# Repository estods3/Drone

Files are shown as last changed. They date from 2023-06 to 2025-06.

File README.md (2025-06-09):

# Quadcopter with ROS/Wifi Flight Controller
This project is for a quadcopter using a WiFi controlled flight controller that you can control from your phone. The flight controller also interfaces with Robotic Operating System (ROS) to support live debugging and data logging with open-sourced industry tools.

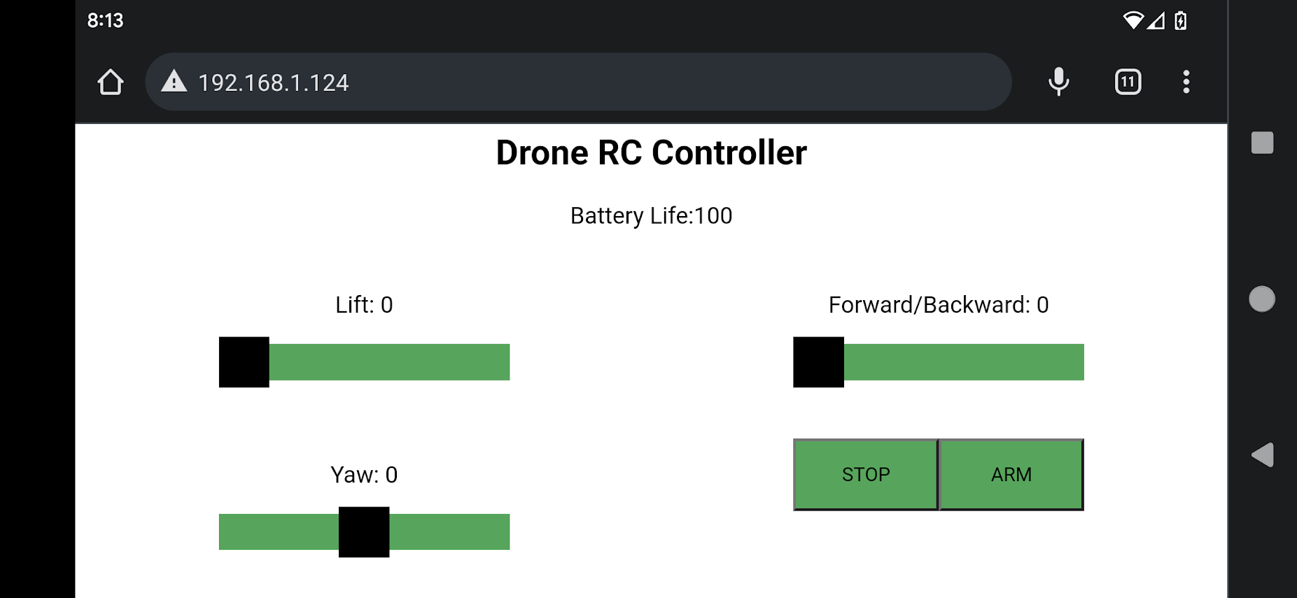
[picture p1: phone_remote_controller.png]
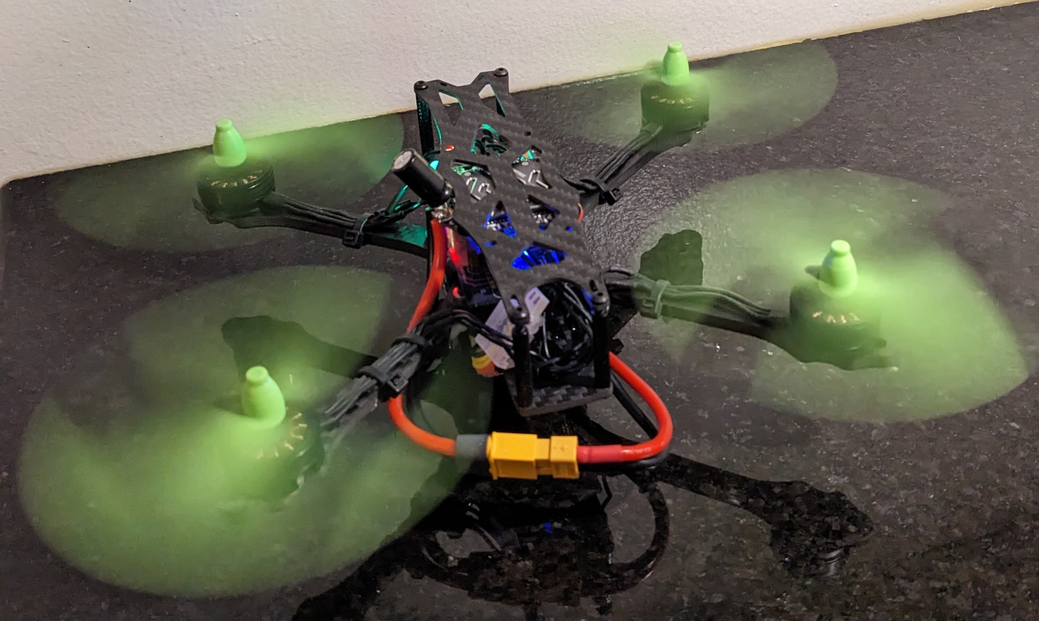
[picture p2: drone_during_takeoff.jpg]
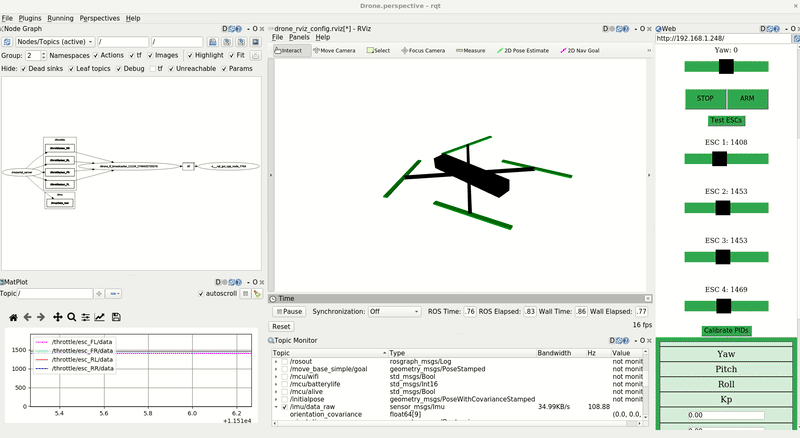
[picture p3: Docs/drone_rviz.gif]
&nbsp;&nbsp;&nbsp;&nbsp;&nbsp;&nbsp;

&nbsp;&nbsp;&nbsp;&nbsp;&nbsp;&nbsp;&nbsp;&nbsp;&nbsp;&nbsp;&nbsp;&nbsp;&nbsp;&nbsp;&nbsp;*Control from Phone/Web, Send Commands to Drone, View data live using ROS*

This repo provides the design files for the custom flight controller hardware and software as well as a parts list for building a working quadcopter with the custom flight controller.

## Flight Controller
The flight controller is a single-board design with accelerometers, microcontroller, wifi, battery monitoring, ESC connector, and status LEDs.

| Top | Bottom |
|---|---|
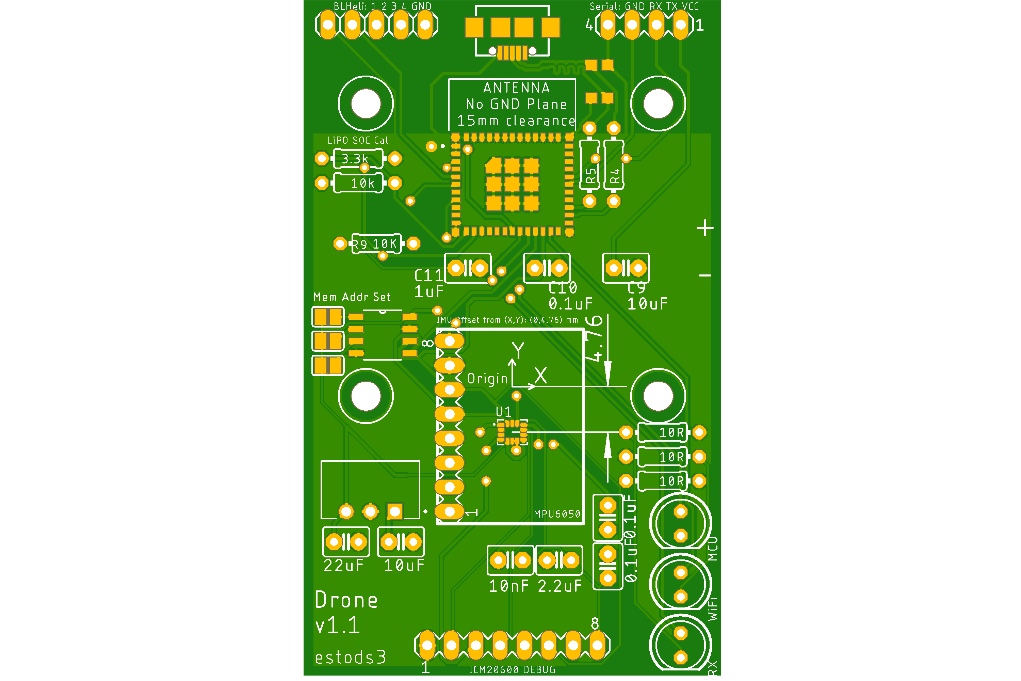
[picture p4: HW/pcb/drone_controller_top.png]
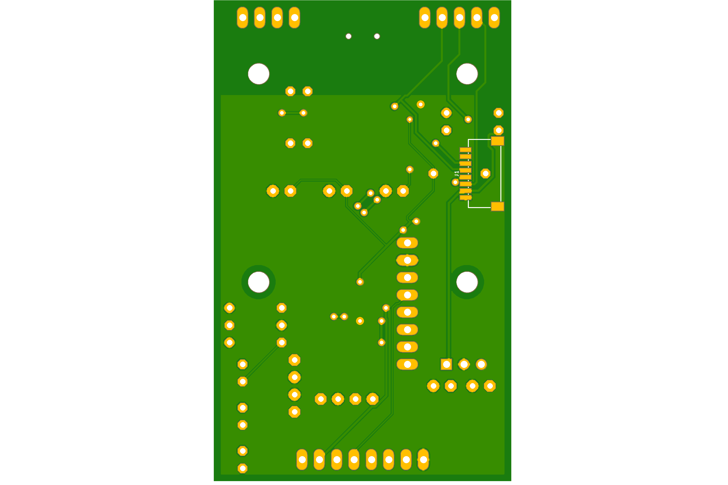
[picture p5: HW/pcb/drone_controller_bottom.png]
|  |  |

Gerber files used to order this PCB are included in the latest release, [here](https://github.com/estods3/Drone/releases/tag/V1.0)

Parts list to assembly final board can be found in the BOM, [here](https://github.com/estods3/Drone/blob/main/HW/BOM.md)

### Hardware Features:
1. 2-Layer design with top and bottom ground plane.
2. Antenna clearance complies with ESP32 specification to help prevent interference to WiFi Signal.
3. IMU orientation aligned with drone frame. Design supports both ISO-20600 and MPU2060 IMU components.

4. Standard 30.5mm by 30.5mm flight controller mounting pattern
5. Eectrical interface using JST-SH 8 Pin connector (compatible with SpeedyBee BL32 50A V3 ESC for stacked ESC/Flight Controller layout).
6. Single Supply (3S LiPo) powering both ESC as well as flight controller (Powered through JST-SH Connector).
7. Status LEDs to quickly see if Wifi is connected, if software is recieving commands from remote controller, etc.
8. Built-in ESC Firmware debug interface with BLHeli Suite (Coming Soon).

### Software Features:
1. Arduino-based C++.
2. Wifi controlled using a phone with browser, provides battery life status as well as controls for Up, Down, Left, Right, etc.
3. Robotic Operating System (ROS) interface provides live feed of IMU data, flight controller status, user commands, and ESC throttle to each motor. (must have variable USE_ROS = True).
4. PID-based flight stability controller (Coming Soon).
5. "Testing Mode" allows user to test throttle of each motor, calibrate PID controller without reflashing flight controller (Coming Soon).

#### IMU Calibration:
Run script to compute IMU calibration:

```
Reading sensors for first time...
Results of measurements a/g:	0.23	0.53	12.09	-0.03	-0.02	0.01

Calculating offsets...
Results of measurements a/g:	-0.00	-0.00	9.81	0.00	0.00	0.00
...

Calibration successful!
Results of measurements a/g:	-0.01	0.00	9.81	0.00	0.00	-0.00

FINISHED!

Sensor readings with offsets:	-0.01	0.00	9.81	0.00	0.00	-0.00
Your offsets:	-0.23	-0.53	-2.29	0.03	0.02	-0.01
```

#### ROS Interface:
Create a ROS interface where you can view and log data from your quadcopter live.

From a PC with ROS installed, run:

```
roscore
```

In another terminal from PC run:

```
roslaunch rosserial_server socket.launch

```

This will create a rosserial server to interface with the nodeMCU controller.

In another terminal launch:
```
rqt
```

to see the following visualization of your drone's data!



#### User Interface/Remote Control
The UI for remote control is deployed over WiFi to a static IP address accessible to a phone logged on to the Flight Controller's hosted WiFi network.



Commands available:

Up, Down, Left, Right, Forward, Backward, Rotate Left, Rotate Right

If not command is given, the drone will hold in place.

## Prototype
This flight controller was tested with a 5 inch FPV Frame, although other frames could be used with tuning of the flight controller.

#### Test Quadcopter Specs:

Physical Size: ~450 grams, 5 inch FPV

Frame: 

Battery Size: 3S Lipo

Motors: brushless DC

ESC: [Speedybee 4-in-1 ESC](https://www.speedybee.com/speedybee-f7-v3-bl32-50a-4-in-1-esc/)

For full BOM, click [here](https://github.com/estods3/Drone/blob/main/HW/BOM.md)

#### ESC Firmware with BLHeli:
Using Arduino Nano as an interface (4wArduino_Nano__16_MULTIv20005.hex) with ESC plugged into pin D4. The opposite corner motors were set to clockwise and counter-clockwise, respectively. NOTE: this can be done in BLHeli software to correct the direction of the motor if the motor was wired incorrectly to the ESC. Brushless DC motors have 3 wires A, B, and C and the order determines the direction.

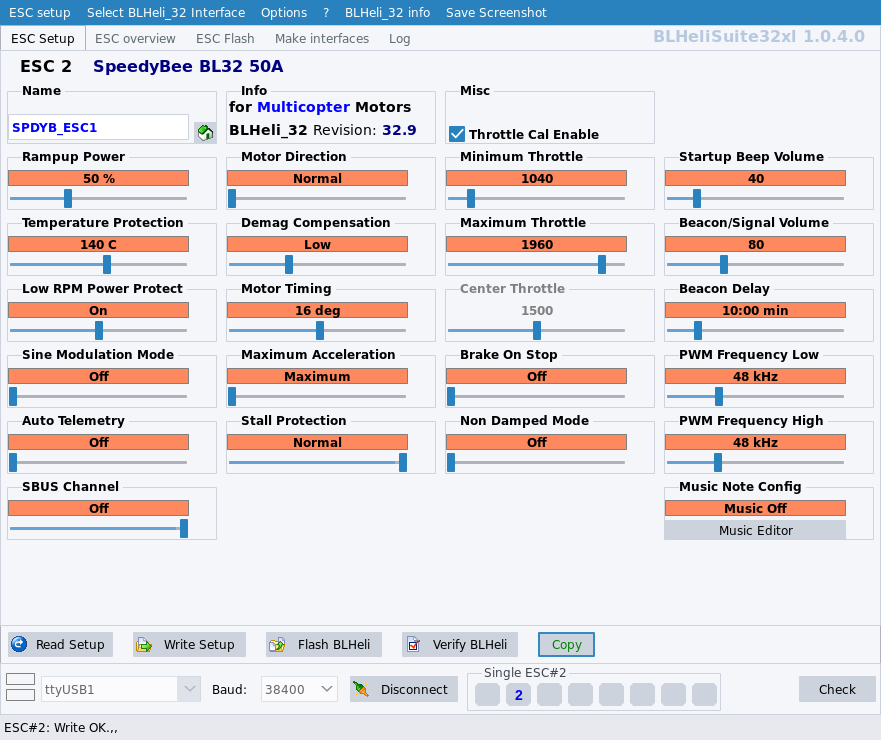
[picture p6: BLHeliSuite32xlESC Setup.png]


## Resources:
PID Controller: 
https://github.com/0xekez/arduino-drone-pid/blob/master/pid_v2_in_arduino/pid_v2_in_arduino.ino
https://www.youtube.com/watch?v=hGcGPUqB67Q
https://www.youtube.com/watch?v=wkfEZmsQqiA
https://github.com/bolandrm/rmb_multicopter

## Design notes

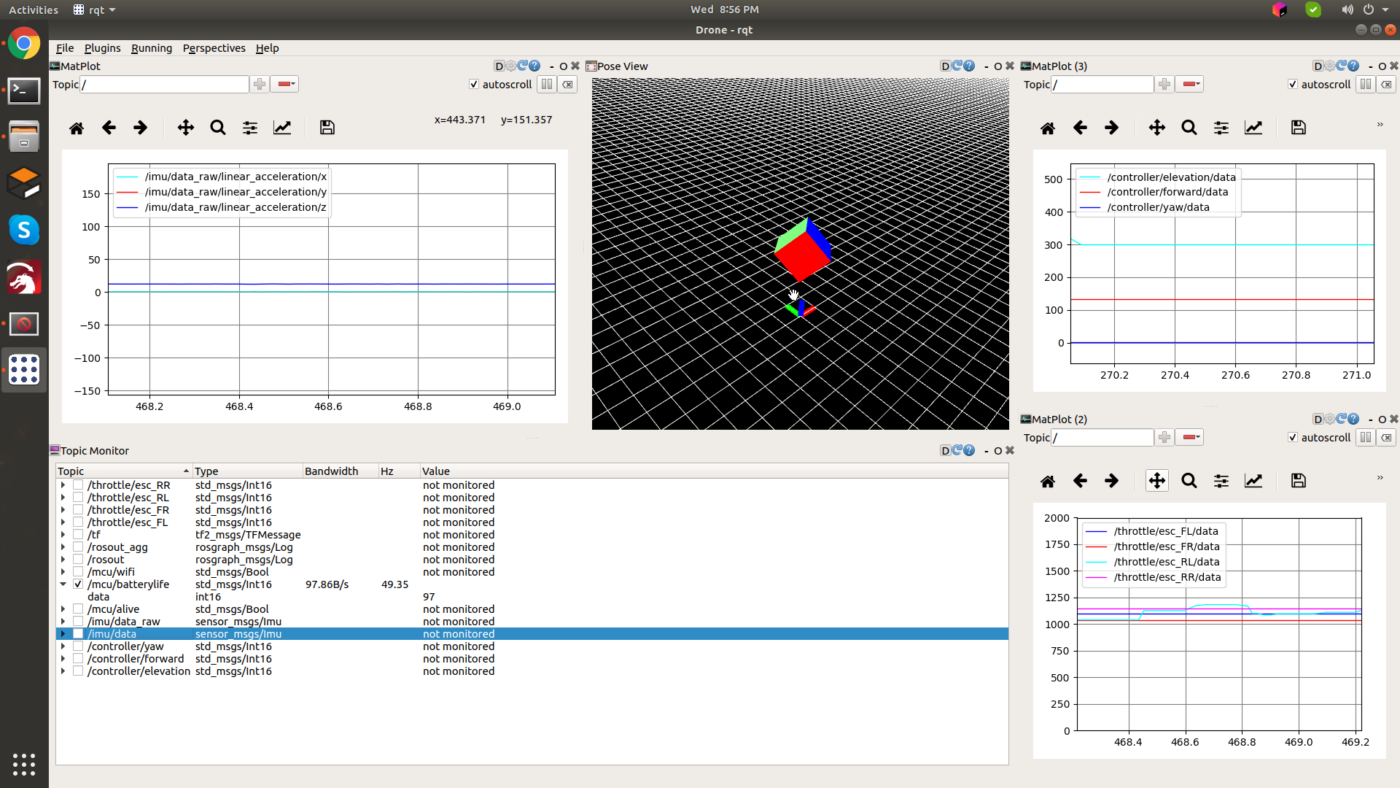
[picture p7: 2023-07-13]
ros_live_visualization.png

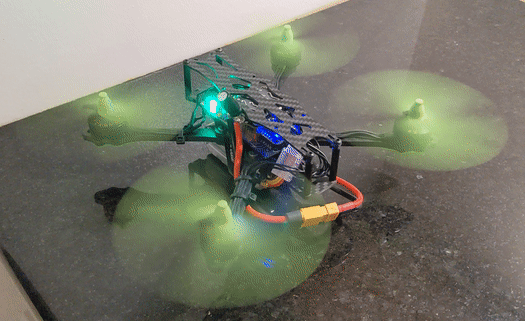
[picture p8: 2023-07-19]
drone.gif

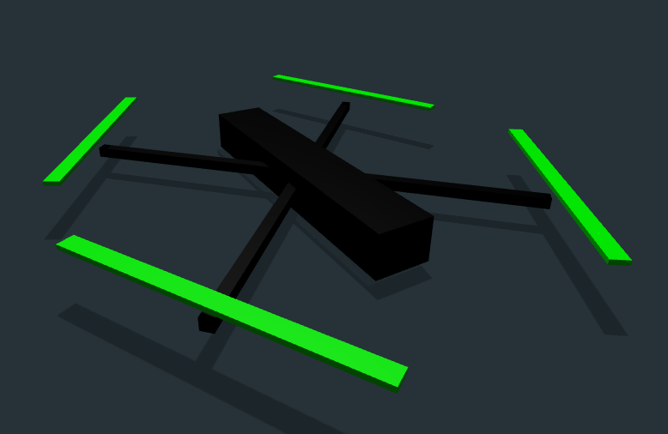
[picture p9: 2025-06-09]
Docs/drone_urdf.png

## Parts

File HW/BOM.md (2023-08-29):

# Bill of Materials

## Powertrain Parts
| Name | Link | Quantity | Part Cost |
| :--- | :--- | :--- | :---- |
| 4-in-1 ESC | [Speedybee](https://www.speedybee.com/speedybee-f7-v3-bl32-50a-4-in-1-esc/) | 1 | $62.99 |
| 3S LiPo Battery | [Amazon - 2 pack](https://www.amazon.com/dp/B07Y67MKQB?psc=1&ref=ppx_yo2ov_dt_b_product_details) | 1 | $30.59 |
| Motors | [Amazon - 4 pack](https://www.amazon.com/dp/B07ZCL45RR?psc=1&ref=ppx_yo2ov_dt_b_product_details) | 4 | $35.99 |
| Propellers | [HobbyKing - 4 pack](https://hobbyking.com/en_us/diatone-5030-plastic-self-tightening-propellers-5-x-3-cw-ccw-green-2-pairs.html) | 4 | $0.67 |
| TOTAL: | | | $130.24 |

## Flight Controller Parts

| Name | Link | Quantity | Part Cost |
| :--- | :--- | :--- | :---- |
| 3.3V Voltage Regulator | [Digikey](https://www.digikey.com/en/products/detail/cui-inc/PXO7803-500-S/16927860) | 1 | $1.41 |
| ESP32 | [Digikey](https://www.digikey.com/en/products/detail/espressif-systems/ESP32-C3-MINI-1-N4/13877574) | 1 | $1.80 |
| IMU1 - ISO20600 | [Digikey](https://www.digikey.com/en/products/detail/tdk-invensense/ICM-20600/8544628) | 1 | $5.67 |
| IMU2 - MPU6050 | [Amazon](https://www.amazon.com/WWZMDiB-Module%EF%BC%883-Axis-Gyroscope-Acceleration%EF%BC%89IIC-Transmission/dp/B0BTKW7K1B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) | 1 | $9.99 |
| JST-SH 8 pin | [HobbyKing - 5 pack](https://hobbyking.com/en_us/jst-sh-8pin-socket-surface-mount-5pcs.html) | 1 | $0.72 |
| micro USB | [Digikey](https://www.digikey.com/en/products/detail/amphenol-cs-fci/10118192-0001LF/2785387) | 1 | $0.40 |
| Memory | [Digikey](https://www.digikey.com/en/products/detail/stmicroelectronics/M24C02-WMN6TP/1663568) | 1 | $0.17 |
| 8-pin header |  | 2 |  |
| 5MM LED |  | 3 |  |
| 10 Ohm Resistor |  | 3 |  |
| 3.3k Ohm Resistor |  | 1 |  |
| 10k Ohm Resistor |  | 1 |  |
| 0.1uF Capacitor |  | 2 |  |
| 10uF Capacitor |  | 1 |  |
| 10nF Capacitor |  | 1 |  |
| 2.2uF Capacitor |  | 1 |  |
| 22uF Capacitor |  | 1 |  |
| TOTAL: |  |  | $20.00 |

NOTE: PCB costs ~$10.00/board to print (Source: Oshpark)

## Frame Parts

| Name | Link | Quantity | Part Cost |
| :--- | :--- | :--- | :---- |
| FPV Racing Drone Frame 5 inch | [Amazon](https://www.amazon.com/gp/product/B071HL5V3H/ref=ppx_yo_dt_b_asin_title_o00_s00?ie=UTF8&psc=1) | 1 | 31.99 |

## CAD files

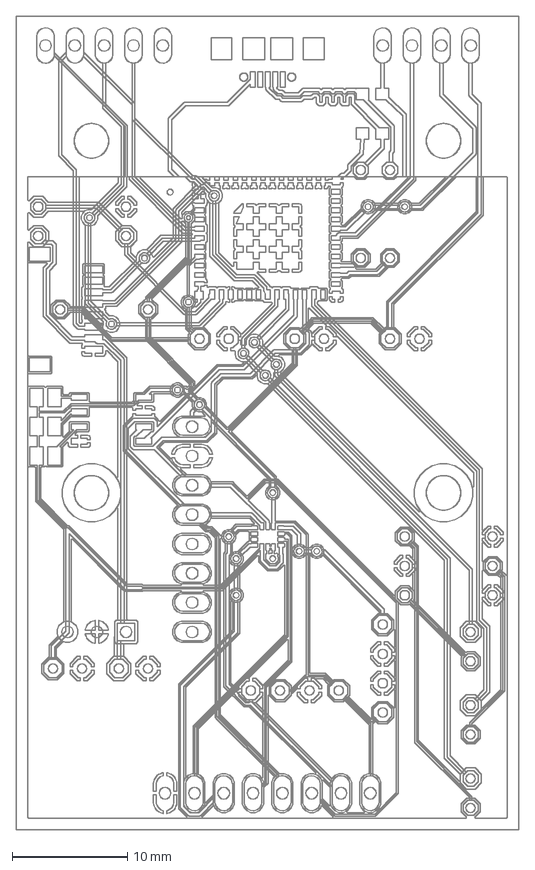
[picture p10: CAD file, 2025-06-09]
HW/pcb/drone_controller_bottom.dxf
43.5 x 70.5 mm

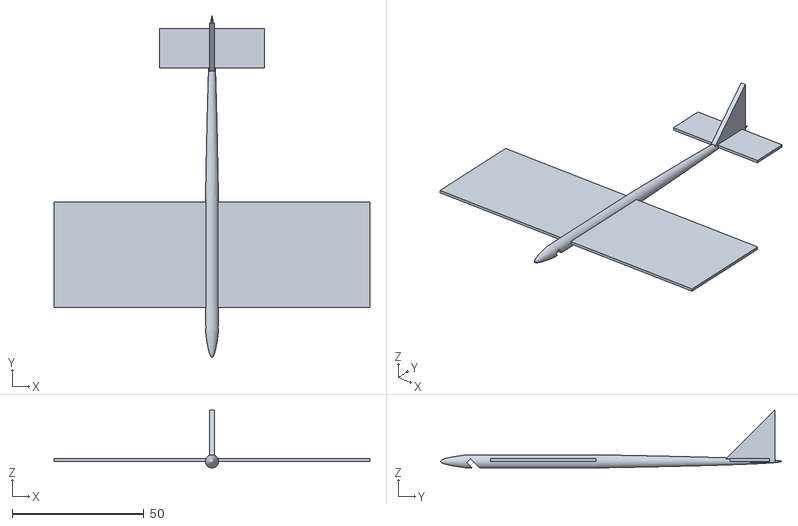
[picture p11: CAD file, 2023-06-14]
SW/orientations_from_IMU_MPU_6050/src/mpu_6050_driver/mesh/FUGMJ38JX8T7E5A.stl
120.0 x 129.5 x 22.0

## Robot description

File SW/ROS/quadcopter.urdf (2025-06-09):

<?xml version="1.0"?>
<robot name="quadcopter_x">

  <!-- Base Link (Main Body) -->
  <link name="base_link">
    <visual>
      <origin xyz="0 0 0" rpy="0 0 0"/>
      <geometry>
        <box size="0.15 0.0254 0.02"/>
      </geometry>
      <material name="body_material">
        <color rgba="0.0 0.0 0.0 1.0"/>
      </material>
    </visual>
    <collision>
      <origin xyz="0 0 0" rpy="0 0 0"/>
      <geometry>
        <box size="0.15 0.0254 0.02"/>
      </geometry>
    </collision>
    <inertial>
      <origin xyz="0 0 0" rpy="0 0 0"/>
      <mass value="0.5"/>
      <inertia ixx="0.001" ixy="0" ixz="0" iyy="0.001" iyz="0" izz="0.001"/>
    </inertial>
  </link>

  <!-- Front Right Arm -->
  <link name="arm_front_right">
    <visual>
      <origin xyz="0.055 0 0" rpy="0 0 0"/>
      <geometry>
        <box size="0.11 0.005 0.005"/>
      </geometry>
      <material name="arm_material">
        <color rgba="0.0 0.0 0.0 1.0"/>
      </material>
    </visual>
    <collision>
      <origin xyz="0.055 0 0" rpy="0 0 0"/>
      <geometry>
        <box size="0.11 0.005 0.005"/>
      </geometry>
    </collision>
    <inertial>
      <origin xyz="0.055 0 0" rpy="0 0 0"/>
      <mass value="0.02"/>
      <inertia ixx="0.0001" ixy="0" ixz="0" iyy="0.0001" iyz="0" izz="0.0001"/>
    </inertial>
  </link>

  <!-- Front Left Arm -->
  <link name="arm_front_left">
    <visual>
      <origin xyz="0.055 0 0" rpy="0 0 0"/>
      <geometry>
        <box size="0.11 0.005 0.005"/>
      </geometry>
      <material name="arm_material">
        <color rgba="0.0 0.0 0.0 1.0"/>
      </material>
    </visual>
    <collision>
      <origin xyz="0.055 0 0" rpy="0 0 0"/>
      <geometry>
        <box size="0.11 0.005 0.005"/>
      </geometry>
    </collision>
    <inertial>
      <origin xyz="0.055 0 0" rpy="0 0 0"/>
      <mass value="0.02"/>
      <inertia ixx="0.0001" ixy="0" ixz="0" iyy="0.0001" iyz="0" izz="0.0001"/>
    </inertial>
  </link>

  <!-- Rear Right Arm -->
  <link name="arm_rear_right">
    <visual>
      <origin xyz="0.055 0 0" rpy="0 0 0"/>
      <geometry>
        <box size="0.11 0.005 0.005"/>
      </geometry>
      <material name="arm_material">
        <color rgba="0.0 0.0 0.0 1.0"/>
      </material>
    </visual>
    <collision>
      <origin xyz="0.055 0 0" rpy="0 0 0"/>
      <geometry>
        <box size="0.11 0.005 0.005"/>
      </geometry>
    </collision>
    <inertial>
      <origin xyz="0.055 0 0" rpy="0 0 0"/>
      <mass value="0.02"/>
      <inertia ixx="0.0001" ixy="0" ixz="0" iyy="0.0001" iyz="0" izz="0.0001"/>
    </inertial>
  </link>

  <!-- Rear Left Arm -->
  <link name="arm_rear_left">
    <visual>
      <origin xyz="0.055 0 0" rpy="0 0 0"/>
      <geometry>
        <box size="0.11 0.005 0.005"/>
      </geometry>
      <material name="arm_material">
        <color rgba="0.0 0.0 0.0 1.0"/>
      </material>
    </visual>
    <collision>
      <origin xyz="0.055 0 0" rpy="0 0 0"/>
      <geometry>
        <box size="0.11 0.005 0.005"/>
      </geometry>
    </collision>
    <inertial>
      <origin xyz="0.055 0 0" rpy="0 0 0"/>
      <mass value="0.02"/>
      <inertia ixx="0.0001" ixy="0" ixz="0" iyy="0.0001" iyz="0" izz="0.0001"/>
    </inertial>
  </link>

  <!-- Propeller Links -->
  <link name="prop_front_right">
    <visual>
      <origin xyz="0 0 0" rpy="0 0 0"/>
      <geometry>
        <box size="0.12 0.007 0.002"/>
      </geometry>
      <material name="prop_material">
        <color rgba="0.0 0.8 0.0 1.0"/>
      </material>
    </visual>
    <collision>
      <origin xyz="0 0 0" rpy="0 0 0"/>
      <geometry>
        <box size="0.12 0.007 0.002"/>
      </geometry>
    </collision>
    <inertial>
      <origin xyz="0 0 0" rpy="0 0 0"/>
      <mass value="0.01"/>
      <inertia ixx="0.00001" ixy="0" ixz="0" iyy="0.00001" iyz="0" izz="0.00001"/>
    </inertial>
  </link>

  <link name="prop_front_left">
    <visual>
      <origin xyz="0 0 0" rpy="0 0 0"/>
      <geometry>
        <box size="0.12 0.007 0.002"/>
      </geometry>
      <material name="prop_material">
        <color rgba="0.0 0.8 0.0 1.0"/>
      </material>
    </visual>
    <collision>
      <origin xyz="0 0 0" rpy="0 0 0"/>
      <geometry>
        <box size="0.12 0.007 0.002"/>
      </geometry>
    </collision>
    <inertial>
      <origin xyz="0 0 0" rpy="0 0 0"/>
      <mass value="0.01"/>
      <inertia ixx="0.00001" ixy="0" ixz="0" iyy="0.00001" iyz="0" izz="0.00001"/>
    </inertial>
  </link>

  <link name="prop_rear_right">
    <visual>
      <origin xyz="0 0 0" rpy="0 0 0"/>
      <geometry>
        <box size="0.12 0.007 0.002"/>
      </geometry>
      <material name="prop_material">
        <color rgba="0.0 0.8 0.0 1.0"/>
      </material>
    </visual>
    <collision>
      <origin xyz="0 0 0" rpy="0 0 0"/>
      <geometry>
        <box size="0.12 0.007 0.002"/>
      </geometry>
    </collision>
    <inertial>
      <origin xyz="0 0 0" rpy="0 0 0"/>
      <mass value="0.01"/>
      <inertia ixx="0.00001" ixy="0" ixz="0" iyy="0.00001" iyz="0" izz="0.00001"/>
    </inertial>
  </link>

  <link name="prop_rear_left">
    <visual>
      <origin xyz="0 0 0" rpy="0 0 0"/>
      <geometry>
        <box size="0.12 0.007 0.002"/>
      </geometry>
      <material name="prop_material">
        <color rgba="0.0 0.8 0.0 1.0"/>
      </material>
    </visual>
    <collision>
      <origin xyz="0 0 0" rpy="0 0 0"/>
      <geometry>
        <box size="0.12 0.007 0.002"/>
      </geometry>
    </collision>
    <inertial>
      <origin xyz="0 0 0" rpy="0 0 0"/>
      <mass value="0.01"/>
      <inertia ixx="0.00001" ixy="0" ixz="0" iyy="0.00001" iyz="0" izz="0.00001"/>
    </inertial>
  </link>

  <!-- Joints connecting arms to body -->
  <joint name="arm_front_right_joint" type="fixed">
    <parent link="base_link"/>
    <child link="arm_front_right"/>
    <origin xyz="0 0 0" rpy="0 0 0.7854"/>
  </joint>

  <joint name="arm_front_left_joint" type="fixed">
    <parent link="base_link"/>
    <child link="arm_front_left"/>
    <origin xyz="0 0 0" rpy="0 0 2.3562"/>
  </joint>

  <joint name="arm_rear_right_joint" type="fixed">
    <parent link="base_link"/>
    <child link="arm_rear_right"/>
    <origin xyz="0 0 0" rpy="0 0 -0.7854"/>
  </joint>

  <joint name="arm_rear_left_joint" type="fixed">
    <parent link="base_link"/>
    <child link="arm_rear_left"/>
    <origin xyz="0 0 0" rpy="0 0 -2.3562"/>
  </joint>

  <!-- Joints connecting propellers to arms -->
  <joint name="prop_front_right_joint" type="continuous">
    <parent link="arm_front_right"/>
    <child link="prop_front_right"/>
    <origin xyz="0.11 0 0.01" rpy="0 0 0"/>
    <axis xyz="0 0 1"/>
  </joint>

  <joint name="prop_front_left_joint" type="continuous">
    <parent link="arm_front_left"/>
    <child link="prop_front_left"/>
    <origin xyz="0.11 0 0.01" rpy="0 0 0"/>
    <axis xyz="0 0 1"/>
  </joint>

  <joint name="prop_rear_right_joint" type="continuous">
    <parent link="arm_rear_right"/>
    <child link="prop_rear_right"/>
    <origin xyz="0.11 0 0.01" rpy="0 0 0"/>
    <axis xyz="0 0 1"/>
  </joint>

  <joint name="prop_rear_left_joint" type="continuous">
    <parent link="arm_rear_left"/>
    <child link="prop_rear_left"/>
    <origin xyz="0.11 0 0.01" rpy="0 0 0"/>
    <axis xyz="0 0 1"/>
  </joint>

</robot>

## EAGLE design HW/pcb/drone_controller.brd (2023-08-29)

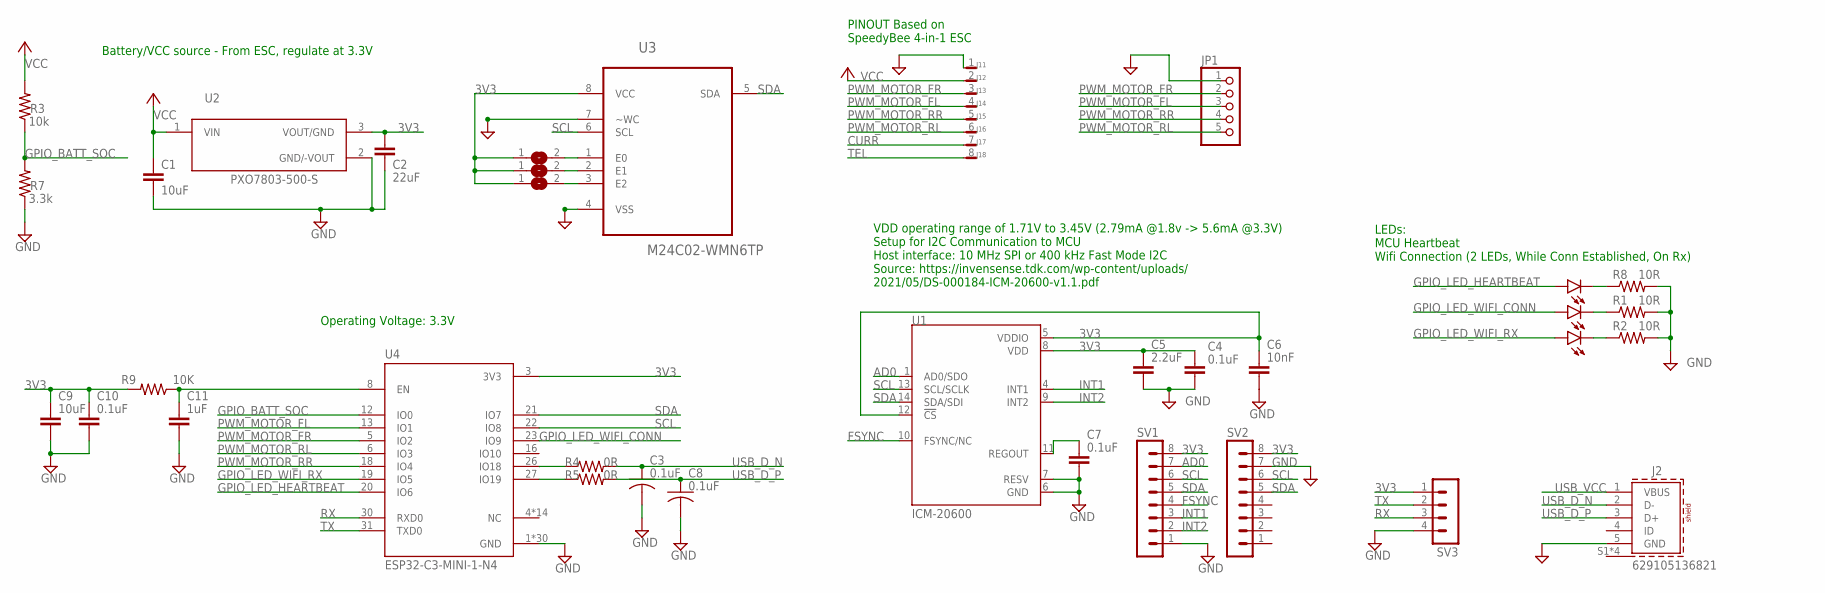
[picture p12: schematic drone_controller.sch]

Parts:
C1, C9: 10uF; C2.5-3
C2: 22uF; C2.5-3
C3, C8: 0.1uF; C0603
C4, C7, C10: 0.1uF; C2.5-3
C5: 2.2uF; C2.5-3
C6: 10nF; C2.5-3
C11: 1uF; C2.5-3
J1: SM08B-SRSS-TB
J2: 629105136821
JP1: PINHD-1X5; 1X05
LED4, LED5, LED6: LED5MM
R1, R2, R8: 10R; 0204/7
R3: 10k; 0204/7
R4, R5: 0R; 0204/7
R7: 3.3k; 0204/7
R9: 10K; 0204/7
SJ1, SJ2, SJ3: SJ
SV1, SV2: MA08-1
SV3: MA04-1
U1: ICM-20600; PQFN50P250X300X97-14N
U2: PXO7803-500-S; CONV_PXO7803-500-S
U3: M24C02-WMN6TP; SOIC127P600X175-8N
U4: ESP32-C3-MINI-1-N4; XCVR_ESP32-C3-MINI-1-N4

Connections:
3V3: C2.1, C4.1, C5.1, C6.1, C9.1, C10.1, R9.2, SJ1.1, SJ2.1, SJ3.1, SV1.8, SV2.8, SV3.1, U1.5 (VDDIO), U1.8 (VDD), U1.12 (!CS), U2.3 (VOUT/GND), U3.8 (VCC), U4.3 (3V3)
AD0: SV1.7, U1.1 (AD0/SDO)
CURR: J1.7
FSYNC: SV1.4, U1.10 (FSYNC/NC)
GND: C1.2, C2.2, C3.2, C4.2, C5.2, C6.2, C7.2, C8.2, C9.2, C10.2, C11.2, J1.1, J2.5 (GND), JP1.1, R1.2, R2.2, R7.1, R8.2, SV1.1, SV2.7, SV3.4, U1.6 (GND), U1.7 (RESV), U2.2 (GND/-VOUT), U3.4 (VSS), U3.7 (~WC), U4.1 (GND), U4.2 (GND), U4.11 (GND), U4.14 (GND), U4.36 (GND), U4.37 (GND), U4.38 (GND), U4.39 (GND), U4.40 (GND), U4.41 (GND), U4.42 (GND), U4.43 (GND), U4.44 (GND), U4.45 (GND), U4.46 (GND), U4.47 (GND), U4.48 (GND), U4.49_1 (GND), U4.49_2 (GND), U4.49_3 (GND), U4.49_4 (GND), U4.49_5 (GND), U4.49_6 (GND), U4.49_7 (GND), U4.49_8 (GND), U4.49_9 (GND), U4.50 (GND), U4.51 (GND), U4.52 (GND), U4.53 (GND)
GPIO_BATT_SOC: R3.1, R7.2, U4.12 (IO0)
GPIO_LED_HEARTBEAT: LED4.A, U4.20 (IO6)
GPIO_LED_WIFI_CONN: LED5.A, U4.23 (IO9)
GPIO_LED_WIFI_RX: LED6.A, U4.19 (IO5)
INT1: SV1.3, U1.4 (INT1)
INT2: SV1.2, U1.9 (INT2)
unnamed: C7.1, U1.11 (REGOUT)
unnamed: C11.1, R9.1, U4.8 (EN)
unnamed: SJ1.2, U3.1 (E0)
unnamed: SJ2.2, U3.2 (E1)
unnamed: SJ3.2, U3.3 (E2)
unnamed: LED5.K (C), R1.1
unnamed: LED4.K (C), R8.1
unnamed: LED6.K (C), R2.1
PWM_MOTOR_FL: J1.4, JP1.3, U4.13 (IO1)
PWM_MOTOR_FR: J1.3, JP1.2, U4.5 (IO2)
PWM_MOTOR_RL: J1.6, U4.6 (IO3)
PWM_MOTOR_RR: J1.5, JP1.4, U4.18 (IO4)
RX: SV3.3, U4.30 (RXD0)
SCL: SV1.6, SV2.6, U1.13 (SCL/SCLK), U3.6 (SCL), U4.22 (IO8)
SDA: SV1.5, SV2.5, U1.14 (SDA/SDI), U3.5 (SDA), U4.21 (IO7)
TEL: J1.8
TX: SV3.2, U4.31 (TXD0)
USB_D_N: C3.1, J2.2 (D-), R4.2
USB_D_P: C8.1, J2.3 (D+), R5.2
USB_RD_N: R4.1, U4.26 (IO18)
USB_RD_P: R5.1, U4.27 (IO19)
USB_VCC: J2.1 (VBUS)
VCC: C1.1, J1.2, R3.2, U2.1 (VIN)

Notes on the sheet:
Battery/VCC source - From ESC, regulate at 3.3V
VDD operating range of 1.71V to 3.45V (2.79mA @1.8v -> 5.6mA @3.3V) Setup for I2C Communication to MCU Host interface: 10 MHz SPI or 400 kHz Fast Mode I2C Source: https://invensense.tdk.com/wp-content/uploads/ 2021/05/DS-000184-ICM-20600-v1.1.pdf
LEDs: MCU Heartbeat Wifi Connection (2 LEDs, While Conn Established, On Rx)
Operating Voltage: 3.3V
PINOUT Based on SpeedyBee 4-in-1 ESC

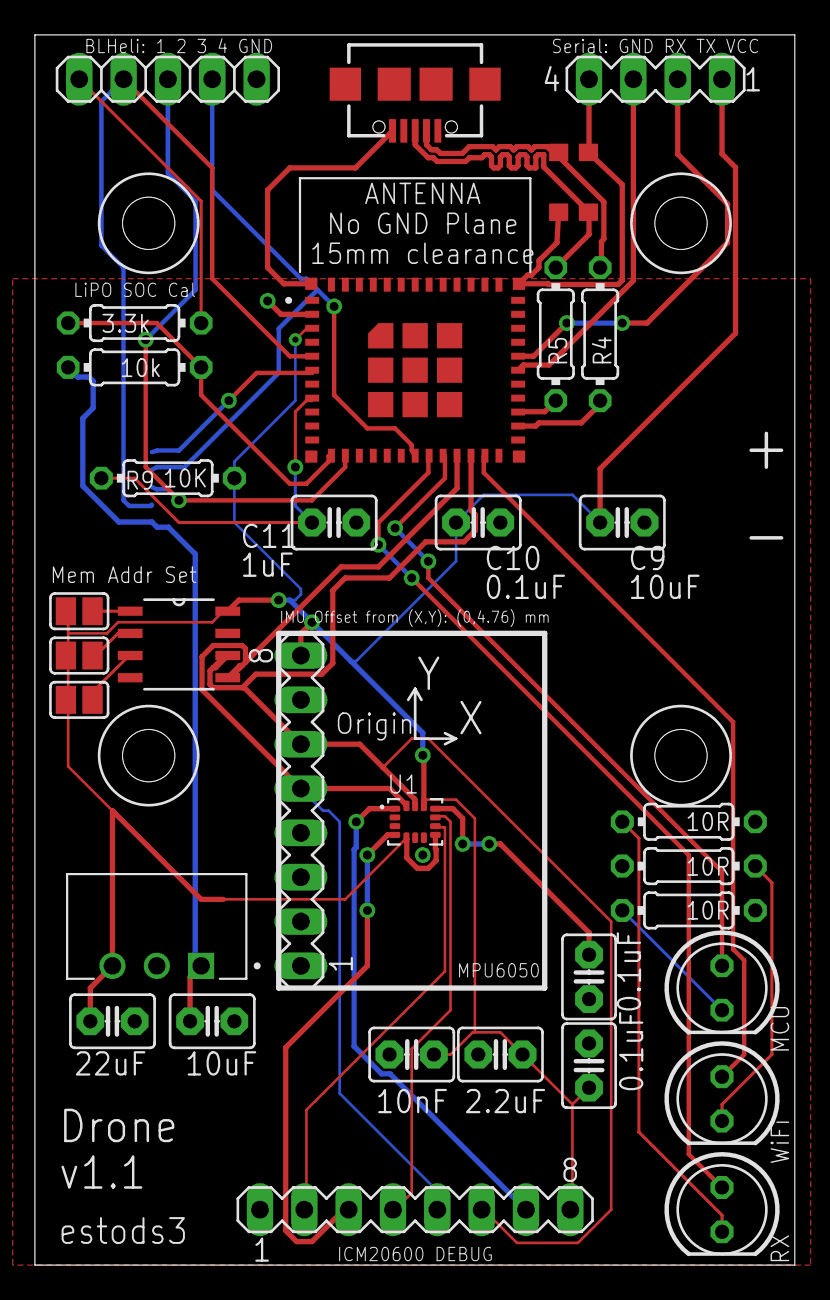
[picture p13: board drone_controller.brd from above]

Board: 2 copper layers, 43.5 x 70.5 mm, 35 parts (1 on the bottom side), 31 nets.

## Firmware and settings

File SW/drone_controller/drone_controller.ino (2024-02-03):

/*
 * Drone Controller
 * github.com/estods3/Drone
 * @author: estods3
 * Description:
 * This SW is the main controller for a NodeMCU-based quadcopter.
  *
 * (A) (B)     x
 *   \ /     z ↑
 *    X       \|
 *   / \       +----→ y
 * (C) (D)
 *
 * Motors A & D run clockwise.
 * Motors B & C run counter-clockwise.
 *
 */
#include <cmath>
#include <ESP8266WiFi.h>
#include <ESPAsyncTCP.h>
#include <ESPAsyncWebServer.h>
#include <ros.h>
#include <ros/time.h>
#include <sensor_msgs/Imu.h>
#include <sensor_msgs/Range.h>
#include <std_msgs/String.h>
#include <std_msgs/Bool.h>
#include <std_msgs/Int16.h>
#include <tf/transform_broadcaster.h>
#include <Adafruit_MPU6050.h>
#include <Adafruit_Sensor.h>
#include <Wire.h>
#include <Servo.h>

// OPERATING MODES
//----------------
#define USE_ROS                     false        // USE_ROS = true, will transmit all data using ROS Serial to a ROS network for remote viewing and logging
#define ACCESS_POINT_WIFI           true       // ACCESS_POINT_WIFI = true, will create a wireless access point called "quadcopter" and allow the user to sign onto that network for RC.

//BMS CALIBRATION
//---------------
// Connect full battery to PCB and check displayed battery level on GUI. Adjust number below until GUI reads 100%.
#define BMS_MAX_BATTERY_BITS		    950         // This number reflects the bit-width of the ADC based on the voltage divider resistors used on PCB. Variation in resistor values is possible.

// ESC CALIBRATION
//-----------------
// These values copied from the BlHeli configuration.
#define ESC_MIN_THROTTLE		        1040
#define ESC_MAX_THROTTLE		        1960
#define ESC_REVERSE_THROTTLE	      100         // NOT USED
#define ESC_ARM_SIGNAL			        1000
#define ESC_ARM_TIME			          2000
#define ESC_DEADZONE_RANGE          100         // NOT USED
#define ESC_FLUTTER_RANGE           10

// IMU CALIBRATION
//----------------
// These values copied from IMU Calibration script.
//-0.23, -0.53, -2.29, 0.03,	0.02, -0.01
#define IMU_CAL_OFFSET1             -0.23
#define IMU_CAL_OFFSET2             -0.53
#define IMU_CAL_OFFSET3             -2.29
#define IMU_CAL_OFFSET4             0.03
#define IMU_CAL_OFFSET5             0.02
#define IMU_CAL_OFFSET6             -0.01

// PINOUT
//-------
// These values are set based on the PCB used.
int gpio_battery_level = A0;
int gpio_esc_pwm_FL = D5;
int gpio_esc_pwm_FR = D6;
int gpio_esc_pwm_RL = D8;
int gpio_esc_pwm_RR = D0; //GPIO16
//NOTE: D0 is the same as the BUILT IN LED pin. The built in LED will pulse opposite D0 PWM Signal.
//NOTE: D0 outputs a HIGH signal at Boot which will turn on the Motor for RR. Need to make sure VCC for motors is disconnected when booting on MCU. 
//Potential Solution: Add RST button circuitry to PCB which triggers reset of NodeMCU + temporarily turns off motor drivers.
int i2c_scl = D1; //USED FOR I2C, comes from hardware variant definition for NodeMCU
int i2c_sda = D2; //USED FOR I2C, comes from hardware variant definition for NodeMCU
int gpio_led_heartbeat = D3;
int gpio_led_wifi_rx = D4;
int gpio_led_wifi_conn = D7; // GPIO13
//NOTE: D4 is the same as the BUILT IN LED pin. The built in LED will pulse opposite D4 HIGH/LOW Status.

// WiFI CALIBRATION
//-----------------
const char* ssid     = "";
const char* password = "";
int wifi_rx_flash_duration_ms = 4;

// Index locations for data and instructions
# define YAW         0
# define PITCH       1
# define ROLL        2
# define THROTTLE    3

# define X           0     // X axis
# define Y           1     // Y axis
# define Z           2     // Z axis

// Status of Drone
# define STOPPED     0
# define ESC_TESTING 1
# define STARTED     2

// ---------------- Control variables ---------------------------------------
float instruction[4] = {0,0,0,0};         // Received flight instructions in order: [Yaw (cardinal direction), Pitch (x), Roll (y), Throttle]

/*
 * Real YPR measurements calculated from combination of accelerometer and gyro data in order: [yaw, pitch, roll]
 *  - Left side up implies positive roll
 *  - Nose up implies positive pitch
 *  - Nose right implies a positive yaw
 */
float measures[3] = {0,0,0};              // Real YPR measurements calculated from combination of accelerometer and gyro data in order: [yaw, pitch, roll]
bool started = false;                     // Flag to signify if the system is started

// ---------------- PID Variables ---------------------------------------
float errors[3];                          // Measured errors compared to target positions in order: [yaw, pitch, roll]
float error_sum[3] = {0,0,0};             // Error sums used for integral component of PID in order: [yaw, pitch, roll]
float previous_error[3] = {0,0,0};        // Previous errors used for derivative component of PID in order: [yaw, pitch, roll]

float Kp[3]        = {0, 0, 0};           // P coefficients in that order : Yaw, Pitch, Roll
float Ki[3]        = {0.00, 0.00, 0.00};  // I coefficients in that order : Yaw, Pitch, Roll
float Kd[3]        = {0, 0, 0};           // D coefficients in that order : Yaw, Pitch, Roll

int status = STOPPED;
// ---------------------------------------------------------------------------

// for calculating running frequency of code
float i {0};
float start_seconds {0};

// GUI Server
//-----------
//WiFiServer gui_server(80);
// Create AsyncWebServer object on port 80
AsyncWebServer server(80);
String batterylife = "100";
String sliderValue1 = "0";
String sliderValue2 = "0";
String sliderValue3 = "0";
String sliderValue4 = String(ESC_MIN_THROTTLE);
String sliderValue5 = String(ESC_MIN_THROTTLE);
String sliderValue6 = String(ESC_MIN_THROTTLE);
String sliderValue7 = String(ESC_MIN_THROTTLE);
int armvalue = 0;
int stopvalue = 0;

const char* PARAM_INPUT = "value";

const char index_html[] PROGMEM = R"rawliteral(
<!DOCTYPE HTML><html>
<head>
  <meta name="viewport" content="width=device-width, initial-scale=1">
  <title>Drone RC Controller</title>
  <style>
    html {font-family: Arial; display: inline-block; text-align: center;}
    h2 {font-size: 1.5rem;}
    p {font-size: 1rem;}
    body {margin:0px auto; padding-bottom: 25px;}
    .slider { -webkit-appearance: none; margin: 1px; width: 200px; height: 25px; background: #32a852;
      outline: none; -webkit-transition: .2s; transition: opacity .2s;}
    .slider::-webkit-slider-thumb {-webkit-appearance: none; appearance: none; width: 35px; height: 35px; background: #000000; cursor: pointer;}
    .slider::-moz-range-thumb { width: 35px; height: 35px; background: #003249; cursor: pointer; }
    .button { width: 100px; height: 50px; background: #32a852; cursor: pointer; }
    .grid-container {
      display: grid;
      grid-template-columns: auto auto;
      padding: 1px;
    }
    .grid-item {
      padding: 10px;
      font-size: 20px;
      text-align: center;
    }
    .PID_grid-container {
      display: grid;
      grid-template-columns: auto auto auto auto;
      background-color: #32a852;
      padding: 10px;
    }
    .PID_grid-item {
      background-color: rgba(255, 255, 255, 0.8);
      border: 1px solid rgba(0, 0, 0, 0.8);
      padding: 5px;
      font-size: 20px;
      text-align: center;
    }
    .collapsible {
      background-color: #32a852;
    }
  </style>
</head>
<body>
  <h2>Drone RC Controller</h2>
  <p>Battery Life:<span id="batterylife">%BATTERYLIFE%</span></p>
  <div class="grid-container">
  <div class="grid-item"><p>Lift: <span id="textSliderValue1">%SLIDER1VALUE%</span></p>
  <p><input type="range" oninput="updateSlider1(this)" id="elevationSlider" min="0" max="%ESC_MAX_THROTTLE%" value="%SLIDER1VALUE%" step="1" class="slider"></p></div>
  <div class="grid-item"><p>Forward/Backward: <span id="textSliderValue3">%SLIDER3VALUE%</span></p>
  <p><input type="range" oninput="updateSlider3(this)" id="forwardSlider" min="-5" max="5" value="%SLIDER3VALUE%" step="1" class="slider"></p></div>
  <div class="grid-item"><p>Yaw: <span id="textSliderValue2">%SLIDER2VALUE%</span></p>
  <p><input type="range" oninput="updateSlider2(this)" id="yawSlider" min="-180" max="180" value="%SLIDER2VALUE%" step="1" class="slider"></p></div>
  <div class="grid-item"><input type="button" id="stop_button" onclick="updateStopButton(this)" value="STOP" class="button"><input type="button"  id="arm_button" onclick="updateArmButton(this)" value="ARM" class="button"></div>  
  </div>
  <button type="button" class="collapsible">Test ESCs</button>
  <div class="content">
    <div class="grid-container">
    <div class="grid-item"><p>ESC 1: <span id="textSliderValue4">%SLIDER4VALUE%</span></p>
    <p><input type="range" oninput="updateSlider4(this)" id="esc1Slider" min="%ESC_MIN_THROTTLE%" max="%ESC_MAX_THROTTLE%" value="%SLIDER4VALUE%" step="1" class="slider"></p></div>
    <div class="grid-item"><p>ESC 2: <span id="textSliderValue5">%SLIDER5VALUE%</span></p>
    <p><input type="range" oninput="updateSlider5(this)" id="esc2Slider" min="%ESC_MIN_THROTTLE%" max="%ESC_MAX_THROTTLE%" value="%SLIDER5VALUE%" step="1" class="slider"></p></div>
    <div class="grid-item"><p>ESC 3: <span id="textSliderValue6">%SLIDER6VALUE%</span></p>
    <p><input type="range" oninput="updateSlider6(this)" id="esc3Slider" min="%ESC_MIN_THROTTLE%" max="%ESC_MAX_THROTTLE%" value="%SLIDER6VALUE%" step="1" class="slider"></p></div>
    <div class="grid-item"><p>ESC 4: <span id="textSliderValue7">%SLIDER7VALUE%</span></p>
    <p><input type="range" oninput="updateSlider7(this)" id="esc4Slider" min="%ESC_MIN_THROTTLE%" max="%ESC_MAX_THROTTLE%" value="%SLIDER7VALUE%" step="1" class="slider"></p></div>
    </div>
  </div>
  <button type="button" class="collapsible">Calibrate PIDs</button>  
  <div class="content">
    <iframe name="dummyframe" id="dummyframe" style="display: none;"></iframe>
    <form action="/PID" target="dummyframe">
      <div class="PID_grid-container">
        <div class="PID_grid-item"></div>
        <div class="PID_grid-item">Yaw</div>
        <div class="PID_grid-item">Pitch</div>
        <div class="PID_grid-item">Roll</div>
        <div class="PID_grid-item">Kp</div>
        <div class="PID_grid-item"><input type="text" id="Kpy" name="Kpy" value="%KPY_VALUE%"><br></div>
        <div class="PID_grid-item"><input type="text" id="Kpp" name="Kpp" value="%KPP_VALUE%"><br></div>
        <div class="PID_grid-item"><input type="text" id="Kpr" name="Kpr" value="%KPR_VALUE%"><br></div>
        <div class="PID_grid-item">Ki</div>
        <div class="PID_grid-item"><input type="text" id="Kiy" name="Kiy" value="%KIY_VALUE%"><br></div>
        <div class="PID_grid-item"><input type="text" id="Kip" name="Kip" value="%KIP_VALUE%"><br></div>
        <div class="PID_grid-item"><input type="text" id="Kir" name="Kir" value="%KIR_VALUE%"><br></div>
        <div class="PID_grid-item">Kd</div>
        <div class="PID_grid-item"><input type="text" id="Kdy" name="Kdy" value="%KDY_VALUE%"><br></div>
        <div class="PID_grid-item"><input type="text" id="Kdp" name="Kdp" value="%KDP_VALUE%"><br></div>
        <div class="PID_grid-item"><input type="text" id="Kdr" name="Kdr" value="%KDR_VALUE%"><br></div>
      </div>
      <input type="submit" value="Submit">
    </form>
  </div>
<script>
var coll = document.getElementsByClassName("collapsible");
var i;

for (i = 0; i < coll.length; i++) {
  coll[i].addEventListener("click", function() {
    this.classList.toggle("active");
    var content = this.nextElementSibling;
    if (content.style.display === "block") {
      content.style.display = "none";
    } else {
      content.style.display = "block";
    }
  });
}
function updateStopButton(element) {
  var xhr1 = new XMLHttpRequest();
  xhr1.open("GET", "/stop?value="+1, true);
  xhr1.send();
}
function updateArmButton(element) {
  var xhr1 = new XMLHttpRequest();
  xhr1.open("GET", "/arm?value="+1, true);
  xhr1.send();
}
function updateSlider1(element) {
  var sliderValue = document.getElementById("elevationSlider").value;
  document.getElementById("textSliderValue1").innerHTML = sliderValue;
  var xhr1 = new XMLHttpRequest();
  xhr1.open("GET", "/slider1?value="+sliderValue, true);
  xhr1.send();
}
function updateSlider2(element) {
  var sliderValue = document.getElementById("yawSlider").value;
  document.getElementById("textSliderValue2").innerHTML = sliderValue;
  var xhr1 = new XMLHttpRequest();
  xhr1.open("GET", "/slider2?value="+sliderValue, true);
  xhr1.send();
}
function updateSlider3(element) {
  var sliderValue = document.getElementById("forwardSlider").value;
  document.getElementById("textSliderValue3").innerHTML = sliderValue;
  var xhr1 = new XMLHttpRequest();
  xhr1.open("GET", "/slider3?value="+sliderValue, true);
  xhr1.send();
}
function updateSlider4(element) {
  var sliderValue = document.getElementById("esc1Slider").value;
  document.getElementById("textSliderValue4").innerHTML = sliderValue;
  var xhr1 = new XMLHttpRequest();
  xhr1.open("GET", "/slider4?value="+sliderValue, true);
  xhr1.send();
}
function updateSlider5(element) {
  var sliderValue = document.getElementById("esc2Slider").value;
  document.getElementById("textSliderValue5").innerHTML = sliderValue;
  var xhr1 = new XMLHttpRequest();
  xhr1.open("GET", "/slider5?value="+sliderValue, true);
  xhr1.send();
}
function updateSlider6(element) {
  var sliderValue = document.getElementById("esc3Slider").value;
  document.getElementById("textSliderValue6").innerHTML = sliderValue;
  var xhr1 = new XMLHttpRequest();
  xhr1.open("GET", "/slider6?value="+sliderValue, true);
  xhr1.send();
}
function updateSlider7(element) {
  var sliderValue = document.getElementById("esc4Slider").value;
  document.getElementById("textSliderValue7").innerHTML = sliderValue;
  var xhr1 = new XMLHttpRequest();
  xhr1.open("GET", "/slider7?value="+sliderValue, true);
  xhr1.send();
}
</script>
</body>
</html>
)rawliteral";

// FUNCTION: Processor
// Replaces placeholder with button section in your web page
String processor(const String& var){
  //Serial.println(var);
  if (var == "BATTERYLIFE"){
    return batterylife;
  }
  if (var == "ESC_MIN_THROTTLE"){
    return String(ESC_MIN_THROTTLE);
  }
  if (var == "ESC_MAX_THROTTLE"){
    return String(ESC_MAX_THROTTLE);
  }
  if (var == "SLIDER1VALUE"){
    return sliderValue1;
  }
  if (var == "SLIDER2VALUE"){
    return sliderValue2;
  }
  if (var == "SLIDER3VALUE"){
    return sliderValue3;
  }
  if (var == "SLIDER4VALUE"){
    return sliderValue4;
  }
  if (var == "SLIDER5VALUE"){
    return sliderValue5;
  }
  if (var == "SLIDER6VALUE"){
    return sliderValue6;
  }
  if (var == "SLIDER7VALUE"){
    return sliderValue7;
  }
  if (var == "KPY_VALUE"){
    return String(Kp[YAW]);
  }
  if (var == "KPP_VALUE"){
    return String(Kp[PITCH]); 
  }
  if (var == "KPR_VALUE"){
    return String(Kp[ROLL]); 
  }
  if (var == "KIY_VALUE"){
    return String(Ki[YAW]);
  }
  if (var == "KIP_VALUE"){
    return String(Ki[PITCH]); 
  }
  if (var == "KIR_VALUE"){
    return String(Ki[ROLL]);
  }
  if (var == "KDY_VALUE"){
    return String(Kd[YAW]);
  }
  if (var == "KDP_VALUE"){
    return String(Kd[PITCH]);
  }
  if (var == "KDR_VALUE"){
    return String(Kd[ROLL]);
  }
  return String();
}

// ROS Interface
//--------------
#ifdef USE_ROS
// Set the rosserial socket server IP address (Same as roscore)
IPAddress ros_socket_server(192, 168, 1, 100);
// Set the rosserial socket server port (default is 11411)
const uint16_t ros_socket_serverPort = 11411;

ros::NodeHandle drone_rosnode_handle;
std_msgs::Bool bool_msg;
ros::Publisher ros_pub_mcu_alive("mcu/alive", &bool_msg);
ros::Publisher ros_pub_mcu_wifi("mcu/wifi", &bool_msg);

sensor_msgs::Imu imu_msg;
ros::Publisher ros_pub_imu("imu/data_raw", &imu_msg);

std_msgs::Int16 int_msg;
ros::Publisher ros_pub_batt_life("mcu/batterylife", &int_msg);

ros::Publisher ros_pub_throttle_esc_FL("throttle/esc_FL", &int_msg);
ros::Publisher ros_pub_throttle_esc_FR("throttle/esc_FR", &int_msg);
ros::Publisher ros_pub_throttle_esc_RL("throttle/esc_RL", &int_msg);
ros::Publisher ros_pub_throttle_esc_RR("throttle/esc_RR", &int_msg);

ros::Publisher ros_pub_command_elev("controller/elevation", &int_msg);
ros::Publisher ros_pub_command_yaw("controller/yaw", &int_msg);
ros::Publisher ros_pub_command_forward("controller/forward", &int_msg);

#endif

// IMU
//----
Adafruit_MPU6050 mpu;

// ESCs
//-----
double rcScaleValue = 1;
Servo esc_FL, esc_FR, esc_RL, esc_RR;
int16_t ESC_FL_CURRENT_INPUT_VALUE, ESC_FR_CURRENT_INPUT_VALUE, ESC_RL_CURRENT_INPUT_VALUE, ESC_RR_CURRENT_INPUT_VALUE = ESC_MIN_THROTTLE;

/*___________________________________________________________________________________________ 
* FUNCTIONS Library
* void connect_to_wifi()
* bool check_wifi_status()
* void initialize_gui_server()
* char get_commands_from_gui_client()
* void initialize_imu()
* struct imu_data read_imu_data(bool log)
* void initialize_ros_serial_socket_server_connection(IPAddress server, uint16_t port)
* 
* ___________________________________________________________________________________________
*/
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
void loop() {
  
  /* Update Variables:
  *  -----------------
  *  Collect Data from various sources such as: heartbeat, wifi status, IMU, GUI
  */
  bool heartbeat_signal = heartbeat.Update();
  bool wifi_connected = check_wifi_status();
  int battery_life = check_battery_life();
  struct imu_data imu_data_set = read_imu_data(false, IMU_CAL_OFFSET1, IMU_CAL_OFFSET2, IMU_CAL_OFFSET3, IMU_CAL_OFFSET4,	IMU_CAL_OFFSET5, IMU_CAL_OFFSET6);
  //char gui_command = get_commands_from_gui_client();
  
  unsigned long sampleMicros = (lastSampleMicros > 0) ? micros() - lastSampleMicros : 0;
  lastSampleMicros = micros();
  angle accelerometer = calculateAccelerometerEulerAngles(imu_data_set);
  angle gyroscope = calculateGyroscopeEulerAngles(imu_data_set, sampleMicros);
  
  /* Flight Controller:
  *  ------------------
  */
  i++;
  readController();
  compute_fused_euler_angles_with_complementaryfilter(gyroscope, accelerometer);
  calculateErrors();
  bool ESC_TESTING_MODE_ACTIVATED = sliderValue4.toInt() > ESC_MIN_THROTTLE || sliderValue5.toInt() > ESC_MIN_THROTTLE || sliderValue6.toInt() > ESC_MIN_THROTTLE || sliderValue7.toInt() > ESC_MIN_THROTTLE;
  if(ESC_TESTING_MODE_ACTIVATED){
    status = ESC_TESTING; 
  }
  Serial.println(String(i/(millis()/1000-start_seconds)) + "  Status: " + String(status) + " YPR: " + String(measures[YAW]) + ", " + String(measures[PITCH]) + ", " + String(measures[ROLL]));

  if(armvalue == 1){
    InitESCs();
    armvalue = 0;
  }
  if(status == ESC_TESTING){
    ESC_FL_CURRENT_INPUT_VALUE = sliderValue4.toInt();
    ESC_FR_CURRENT_INPUT_VALUE = sliderValue5.toInt();
    ESC_RL_CURRENT_INPUT_VALUE = sliderValue7.toInt();
    ESC_RR_CURRENT_INPUT_VALUE = sliderValue6.toInt();
    applyMotorSpeeds();
  }
  if(stopvalue == 1 || status == STOPPED){
    ESC_FL_CURRENT_INPUT_VALUE = 1000;
    ESC_FR_CURRENT_INPUT_VALUE = 1000;
    ESC_RL_CURRENT_INPUT_VALUE = 1000;
    ESC_RR_CURRENT_INPUT_VALUE = 1000;
    stopvalue = 0;
    status = STOPPED;
    sliderValue1 = 0; //TODO - when "stop" clicked, start to gradually lower lift slider until it reaches 0., OR IF wifi connection is lost
    sliderValue2 = 0;
    sliderValue3 = 0;
    sliderValue4 = String(ESC_MIN_THROTTLE);
    sliderValue5 = String(ESC_MIN_THROTTLE);
    sliderValue6 = String(ESC_MIN_THROTTLE);
    sliderValue7 = String(ESC_MIN_THROTTLE);
    stopMotors();
  }
  if (status == STARTED) {
    pidController();
    applyMotorSpeeds();
  }
  delay(1); //Control loop delay

  /* Update ROS Network:
  *  -------------------
  *  Publish Data from various sources such as: heartbeat, wifi status, battery life, IMU, GUI
  *  to ROS Network
  */  
  if(USE_ROS) {
    if(drone_rosnode_handle.connected()) {

      // Publish Heartbeat, Wifi, Battery Life, and Remote Controller
      bool_msg.data = heartbeat_signal;
      ros_pub_mcu_alive.publish(&bool_msg);

      bool_msg.data = wifi_connected;
      ros_pub_mcu_wifi.publish(&bool_msg);

      int_msg.data = battery_life;
      ros_pub_batt_life.publish(&int_msg);

      int_msg.data = int16_t(sliderValue1.toInt());
      ros_pub_command_elev.publish(&int_msg);
      int_msg.data = int16_t(sliderValue2.toInt());
      ros_pub_command_yaw.publish(&int_msg);
      int_msg.data = int16_t(sliderValue3.toInt());
      ros_pub_command_forward.publish(&int_msg);

      // Read each ESC Throttle Value and Publish to ROS Network
      int_msg.data = esc_FL.readMicroseconds();
      ros_pub_throttle_esc_FL.publish(&int_msg);
      int_msg.data = esc_FR.readMicroseconds();
      ros_pub_throttle_esc_FR.publish(&int_msg);
      int_msg.data = esc_RL.readMicroseconds();
      ros_pub_throttle_esc_RL.publish(&int_msg);
      int_msg.data = esc_RR.readMicroseconds();
      ros_pub_throttle_esc_RR.publish(&int_msg);

      double time_in_seconds = drone_rosnode_handle.now().toSec();
      imu_msg.header.frame_id = "/imu_link";
      imu_msg.header.stamp = drone_rosnode_handle.now();
      struct Quaterniond q = toQuaternion(measures[YAW], measures[PITCH], measures[ROLL]);
      imu_msg.orientation.x = q.x;
      imu_msg.orientation.y = q.y;
      imu_msg.orientation.z = q.z;
      imu_msg.orientation.w = q.w;
      imu_msg.angular_velocity.x = imu_data_set.g.gyro.x;
      imu_msg.angular_velocity.y = imu_data_set.g.gyro.y;
      imu_msg.angular_velocity.z = imu_data_set.g.gyro.z;
      imu_msg.linear_acceleration.x = imu_data_set.a.acceleration.x;
      imu_msg.linear_acceleration.y = imu_data_set.a.acceleration.y;
      imu_msg.linear_acceleration.z = imu_data_set.a.acceleration.z;
      ros_pub_imu.publish(&imu_msg);          
    }
    drone_rosnode_handle.spinOnce();
  }
}

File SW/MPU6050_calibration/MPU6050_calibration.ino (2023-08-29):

// Arduino sketch that returns calibration offsets for MPU6050 //   Version 1.1  (31th January 2014)
// Done by Luis Ródenas <luisrodenaslorda@gmail.com>
// Based on the I2Cdev library and previous work by Jeff Rowberg <jeff@rowberg.net>
// Updates (of the library) should (hopefully) always be available at https://github.com/jrowberg/i2cdevlib

// These offsets were meant to calibrate MPU6050's internal DMP, but can be also useful for reading sensors. 
// The effect of temperature has not been taken into account so I can't promise that it will work if you 
// calibrate indoors and then use it outdoors. Best is to calibrate and use at the same room temperature.

/* ==========  LICENSE  ==================================
 I2Cdev device library code is placed under the MIT license
 Copyright (c) 2011 Jeff Rowberg
 
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
 THE SOFTWARE IS PROVIDED "AS IS", WITHOUT WARRANTY OF ANY KIND, EXPRESS OR
 IMPLIED, INCLUDING BUT NOT LIMITED TO THE WARRANTIES OF MERCHANTABILITY,
 FITNESS FOR A PARTICULAR PURPOSE AND NONINFRINGEMENT. IN NO EVENT SHALL THE
 AUTHORS OR COPYRIGHT HOLDERS BE LIABLE FOR ANY CLAIM, DAMAGES OR OTHER
 LIABILITY, WHETHER IN AN ACTION OF CONTRACT, TORT OR OTHERWISE, ARISING FROM,
 OUT OF OR IN CONNECTION WITH THE SOFTWARE OR THE USE OR OTHER DEALINGS IN
 THE SOFTWARE.
 =========================================================
 */

// I2Cdev and MPU6050 must be installed as libraries
//#include "I2Cdev.h"
#include "MPU6050.h"
#include <Adafruit_MPU6050.h>
#include <Adafruit_Sensor.h>
#include "Wire.h"
//#include <EEPROMex.h> // include EEPROM library to write the calibrated offset values into the EEPROM

//#define MEMORYBASEMPUCALIBOFFSET 96 // start storing the calibration values starting at this address
//#define MEMORYBASEMPUCALIBOFFSET 200 // start storing the calibration values starting at this address
#define DEBUGVERBOSE
#define SENSORS_GRAVITY_EARTH (9.80665F) /**< Earth's gravity in m/s^2 */
///////////////////////////////////   CONFIGURATION   /////////////////////////////
//Change this 3 variables if you want to fine tune the skecth to your needs.e
int buffersize=2000;     //Amount of readings used to average, make it higher to get more precision but sketch will be slower  (default:1000)
int discardfirstmeas=100;  // Amount of initial measurements to be discarded
float acel_deadzone=0.01;     //Acelerometer error allowed, make it lower to get more precision, but sketch may not converge  (default:8)
float giro_deadzone=0.01;     //Giro error allowed, make it lower to get more precision, but sketch may not converge  (default:1)
float accel_offset_divisor=1; //8;
float gyro_offset_divisor=1; //4;
// deadzone: amount of variation between 2 consecutive measurements

// default I2C address is 0x68
// specific I2C addresses may be passed as a parameter here
// AD0 low = 0x68 (default for InvenSense evaluation board)
// AD0 high = 0x69
Adafruit_MPU6050 mpu;
//MPU6050 accelgyro(0x69); // <-- use for AD0 high

//int16_t ax, ay, az,gx, gy, gz;

float mean_ax,mean_ay,mean_az,mean_gx,mean_gy,mean_gz,state=0;
float ax_offset,ay_offset,az_offset,gx_offset,gy_offset,gz_offset;
float ax_initoffset,ay_initoffset,az_initoffset,gx_initoffset,gy_initoffset,gz_initoffset;
unsigned int calibratedOffsetAdress = 0;

unsigned int loopcount=0;

// FUNCTION: Initialize IMU
// Description: initialize connection to IMU over I2C
void initialize_imu(){
    // Try to initialize!
  if (!mpu.begin()) {
    Serial.println("Failed to find MPU6050 chip");
    while (1) {
      delay(10);
    }
  }
  Serial.println("MPU6050 Found!");

  mpu.setAccelerometerRange(MPU6050_RANGE_8_G);
  mpu.setGyroRange(MPU6050_RANGE_250_DEG);
  mpu.setFilterBandwidth(MPU6050_BAND_21_HZ);
  mpu.setInterruptPinLatch(true);
  delay(100);
}

struct imu_data{
  sensors_event_t a;
  sensors_event_t g;
  sensors_event_t temp;  
};

// FUNCTION: Read IMU data
// Description: Read IMU data. Log to serial for serial plotter if log= true
struct imu_data read_imu_data(bool log, float o1, float o2, float o3, float o4, float o5, float o6){
  sensors_event_t a, g, temp;
  mpu.getEvent(&a, &g, &temp);
  if(log){
    Serial.print("AccelX:");
    Serial.print(a.acceleration.x);
    Serial.print(",");
    Serial.print("AccelY:");
    Serial.print(a.acceleration.y);
    Serial.print(",");
    Serial.print("AccelZ:");
    Serial.print(a.acceleration.z);
    Serial.print(", ");
    Serial.print("GyroX:");
    Serial.print(g.gyro.x);
    Serial.print(",");
    Serial.print("GyroY:");
    Serial.print(g.gyro.y);
    Serial.print(",");
    Serial.print("GyroZ:");
    Serial.print(g.gyro.z);
    Serial.println("");      
  }

  struct imu_data dataset;
  dataset.a = a;
  dataset.g = g;
  dataset.temp = temp;

  // Apply Calibration
  dataset.a.acceleration.x = dataset.a.acceleration.x + o1;
  dataset.a.acceleration.y = dataset.a.acceleration.y + o2;
  dataset.a.acceleration.z = dataset.a.acceleration.z + o3;
  dataset.g.gyro.x = dataset.g.gyro.x + o4;
  dataset.g.gyro.y = dataset.g.gyro.y + o5;
  dataset.g.gyro.z = dataset.g.gyro.z + o6;

  return dataset;
}

///////////////////////////////////   SETUP   ////////////////////////////////////
void setup() {
  // join I2C bus (I2Cdev library doesn't do this automatically)
  Wire.begin();
  // COMMENT NEXT LINE IF YOU ARE USING ARDUINO DUE
  //TWBR = 24; // 400kHz I2C clock (200kHz if CPU is 8MHz). Leonardo measured 250kHz.

  // initialize serial communication
  Serial.begin(115200);

  // wait for ready
  while (Serial.available() && Serial.read()); // empty buffer
  while (!Serial.available()){
    Serial.println(F("Send any character to start sketch.\n"));
    delay(1500);
  }                
  while (Serial.available() && Serial.read()); // empty buffer again

  // initialize device
  initialize_imu();

  // start message
  Serial.println("\nMPU6050 Calibration Sketch");
  delay(2000);
  Serial.println("\nYour MPU6050 should be placed in horizontal position, with package letters facing up. \nDon't touch it until you see a finish message.\n");
  delay(3000);
  // verify connection
  // reset offsets
  ax_offset = 0;
  ay_offset = 0;
  az_offset = 0;
  gx_offset = 0;
  gy_offset = 0;
  gz_offset = 0;
  ax_initoffset=0;
  ay_initoffset=0;
  az_initoffset=0;
  gx_initoffset=0;
  gy_initoffset=0;
  gz_initoffset=0;  
        
  // Get config from EEPROM if there is one
  // or initialise value with default ones set in StoreStruct
  //EEPROM.setMemPool(MEMORYBASEMPUCALIBOFFSET, EEPROMSizeATmega328); //Set memorypool base, assume Arduino Uno board

}
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

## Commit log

2023-03-16 added BOM
2023-03-16 added test files for tests performed with NodeMCU. Tested LED blinking with GPIO and controlling over WIFI, Accelerometer over I2C and built in LED. Have not yet tested ROS Test talker.py
2023-03-18 updated readme. added LEDs to drone SW
2023-03-19 implemented heartbeat LED in SW. Adjusted position of MCU on board to account for loss from GND plane. Removed unneeded battery indicators (only one LED for Low BATT).
    [drone_controller.brd, drone_controller.sch]
2023-03-20 tested PWM from NodeMCU. working on all pins
2023-03-20 split up functionality into functions. added pinout for LEDs, PWM.
2023-03-20 implemented pinout into schematic. added LED interface
    [drone_controller.brd, drone_controller.sch]
2023-03-22 implemented ros IMU messages. still testing.
2023-03-23 WORKING VERSION: drone controller with ROS reporting heartbeat and IMU data over ROS network. display is working in RQT and populating in RVIZ. more work needed to display in correct coordinate syste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
    [drone_controller.ino]
2023-03-24 Working Version. Drone Controller with IMU, heartbeat, wifi connection status, and command from GUI Server all running simultaniously on target MCU with comms wirelessly with ROS. Host PC running ROS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
2023-06-13 added motor control to drone controller for testing. adding ESC interface using Servo library. added GUI options to Init ESC and +/- throttle for a single ESC. WORKING VERSION on breadboard hardware 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
2023-06-13 working on PCB design. added 3.3v to 5v level shifter, but it is not needed. tested NodeMCU to SpeedyBee ESC and was able to communicate using Servo Library without needed PWM voltage to increase fro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
    [drone_controller.brd, drone_controller.sch]
2023-06-13 added useful test files to testing ESCs and calibrating MPU6050.
2023-06-14 removed 3.3V to 5V level shifter. not needed for this ESC (SpeedyBee 4-in-1 ESC). Placed components on board in more organized layout. Routed Board. All Airwires routed. Added Ground planes with stic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
    [drone_controller.brd, drone_controller.sch]
2023-06-14 implemented battery life into drone controller and GUI. tested and calibrated. working correctly.
    [drone_controller.ino]
2023-06-14 ordered PCB
    [drone_controller.brd]
2023-06-20 Tested IMU with both Arduino Serial logging and ROS. both worked correctly and were being plotted. Did side by side comparison of Serial data and ROS data plotting and both responded to movement of t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
    [drone_controller.ino]
2023-06-20 briefly was able to control ESC with similar code in this commit. seems to be hardware issue with connection to ESC. Also, intermittent connection to MPU IMU. Need to do full hardware test where ESC 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
    [drone_controller.ino]
2023-07-12 implemented new HTML front end for drone controller with CSS and slider bars to adjust throttle for elevation, yaw, and forward/backward. none of these are implemented with PID flight controller yet.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
2023-07-13 added elevation,yaw,and forward/backward controls to ROS and front end. not yet tied into PID controller. Implemented stop and arm buttons on front end and improbed look/feel of front end
2023-07-15 modified IMU calibration script. implemented Adafruit library. tested and imported calibration offsets into main drone_controller code
2023-08-29 ordered V1.1 of drone PCB
    [drone_controller.brd, drone_controller.sch]
2023-12-11 added settings section of UI to allow for updating PID values.
2023-12-11 code cleanup. added new support for measurements from IMU into PID. not yet finished
2023-12-11 working on drone. can mode properly. need to test if it works with motors connected to power
2023-12-18 added 2 wifi modes to allow AccessPoint or connect to existing network (useful for wifi debugging with ROS). Tested with home WIFI and ROS with RQT. all 4 ESCs working and orientation visualization o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
2023-12-19 implemented complementary filter for IMU. working in all 3 dimensions. tested with quarternion function to communicate message onto ROS network
2024-02-03 added front end functionality to pull from currently saved PID cal values. adjusted top throttle setting for lift. adjusted yaw measurement to be negative to match intented coordinate system (in comm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
2025-06-09 added ROS files
    [quadcopter.urdf]
2025-06-09 misc HW file
    [drone_controller_bottom.dxf]

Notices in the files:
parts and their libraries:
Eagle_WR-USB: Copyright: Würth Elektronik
